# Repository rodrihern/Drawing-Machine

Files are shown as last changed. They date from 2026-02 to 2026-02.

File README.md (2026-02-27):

# Drawing Machine

Plotter de dibujo construido junto a 3 compañeros durante el secundario. La máquina mueve un marcador en los ejes X e Y usando motores paso a paso, y sube/baja el marcador con un servo, todo controlado por un Arduino con una CNC Shield.

## Hardware

- Arduino Uno
- CNC Shield con drivers A4988
- 2 motores paso a paso (ejes X e Y)
- 1 servo (eje Z, para subir/bajar el marcador)
- 2 finales de carrera (home X e Y)
- Estructura mecánica propia (ver carpeta `parts3d/`)

El shield fue diseñado en Altium (archivos en `shield/`) y es equivalente al **Arduino CNC Shield v3**

### Área de dibujo

- X: 0 – 228 mm
- Y: 0 – 244 mm

## Software

### Firmware (Arduino)

El archivo principal es [`src/drawing_machine.ino`](src/drawing_machine.ino).  
Recibe comandos G-code por puerto serie (9600 baud) y los ejecuta.  
Al iniciar, la máquina hace homing automático yendo al origen (0, 0) con los finales de carrera.

Parámetros configurables dentro del `.ino`:

| Parámetro | Valor por defecto | Descripción |
|---|---|---|
| `modoDePaso` | 16 (1/16 step) | Microstepping |
| `stepDelay` | `1000 / modoDePaso` | Velocidad de los motores |
| `StepsPerMillimeterX/Y` | `~50.4 steps/mm` | Calibración |
| `penZUp / penZDown` | 90° / 0° | Posición del servo |

### Envío del G-code (Python)

El script [`src/sender.py`](src/sender.py) lee un archivo G-code línea por línea y lo envía al Arduino por serial, esperando confirmación (`ok`) antes de enviar la siguiente línea.

Requiere la librería `pyserial`:

```bash
pip install pyserial
```

Antes de correrlo, ajustar el puerto COM en el script y pasarle la ruta al archivo G-code.

## Flujo de uso

1. **Generar el G-code** en Inkscape con el plugin 4xiDraw. Tutorial: https://www.youtube.com/watch?v=bhzCfIEzs0w

2. **Filtrar arcos** (convertir arcos a segmentos rectos): https://constant-flow.github.io/arc-breaker/

3. **Conectar el Arduino** Copiar y pegar el archivo gcode del dibujo en `drawing_to_send.txt` y correr el script Python:
   ```bash
   python src/sender.py
   ```

## Estructura del repositorio

```
src/        → Firmware Arduino y script Python
parts3d/    → Modelos 3D de las piezas
shield/     → Diseño del PCB (Altium)
drawings/   → G-codes e imágenes de dibujos realizados
```

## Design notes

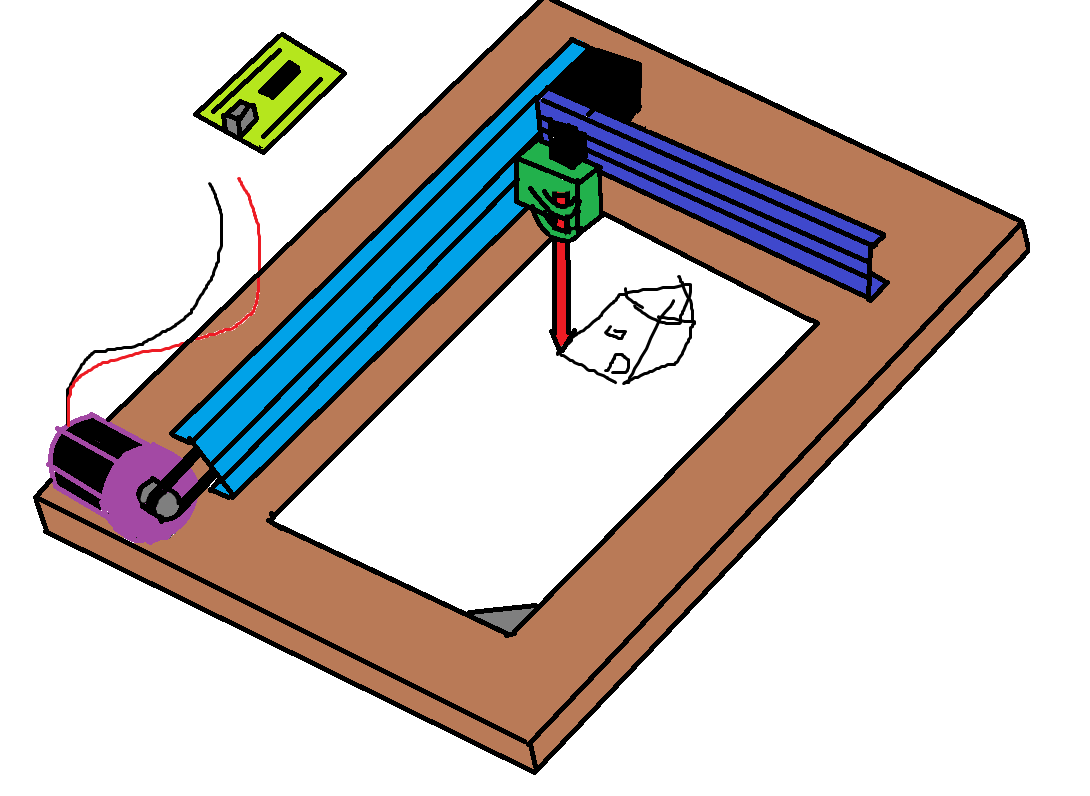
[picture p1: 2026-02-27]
design.png

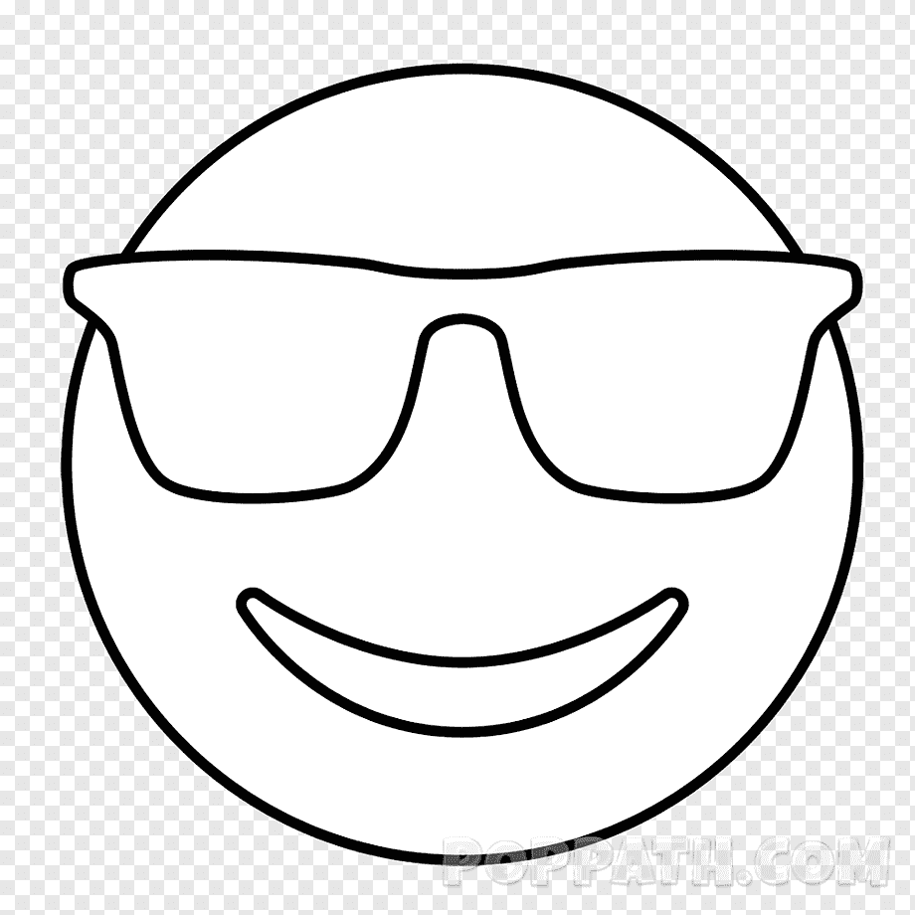
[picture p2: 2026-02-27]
drawings/carita con anteojos.png

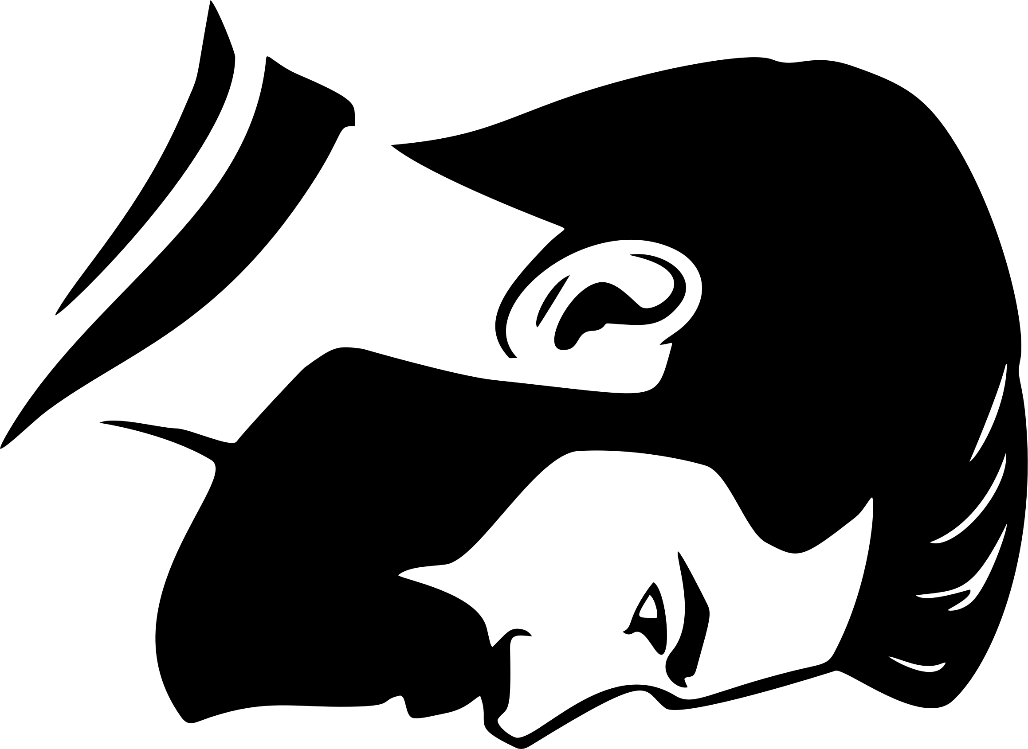
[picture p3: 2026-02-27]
drawings/Gaspi chad.png

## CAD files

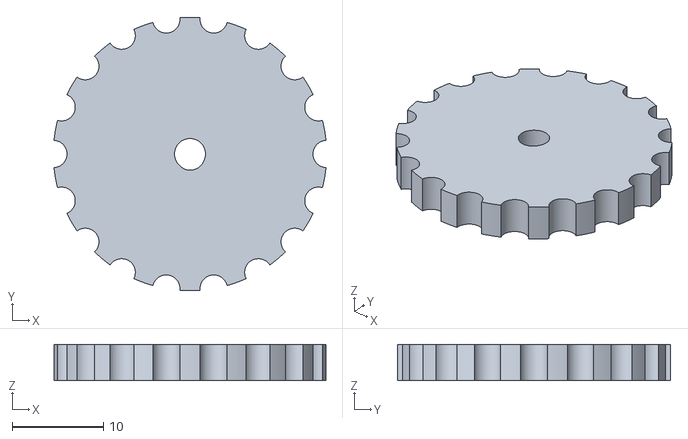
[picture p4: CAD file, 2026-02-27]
parts3d/bed levelling gear.stl
29.9 x 30.0 x 4.00

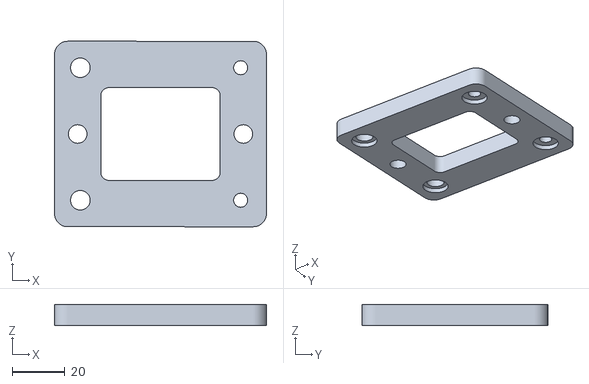
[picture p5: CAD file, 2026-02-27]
parts3d/Intersenction Bottom.stl
80.0 x 70.0 x 8.00

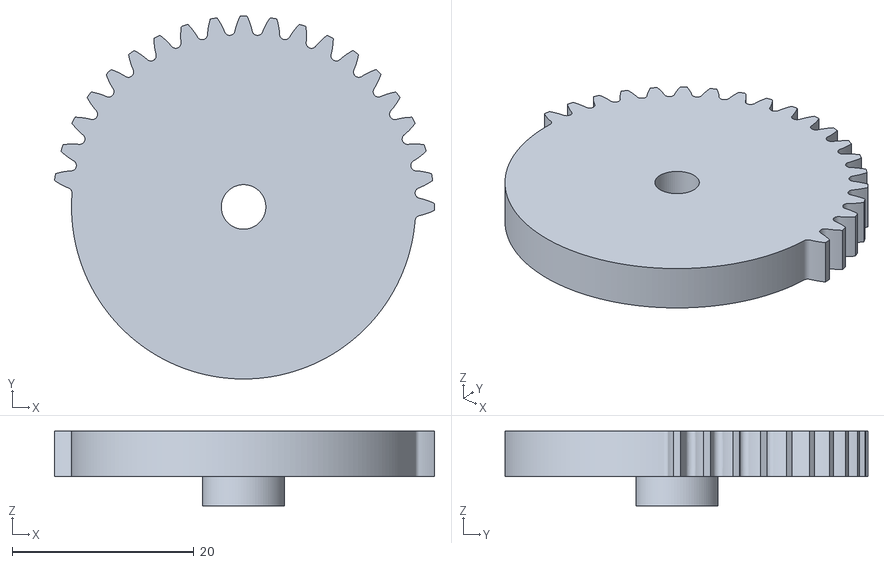
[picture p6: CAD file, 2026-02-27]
parts3d/gear.stl
41.8 x 39.9 x 8.20

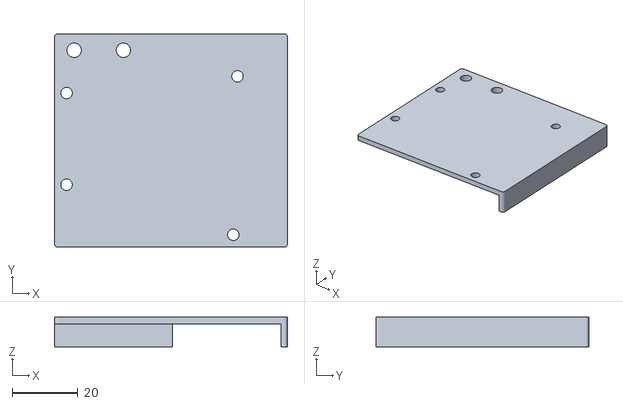
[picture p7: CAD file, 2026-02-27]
parts3d/arduino plate.stl
71.0 x 65.0 x 9.00

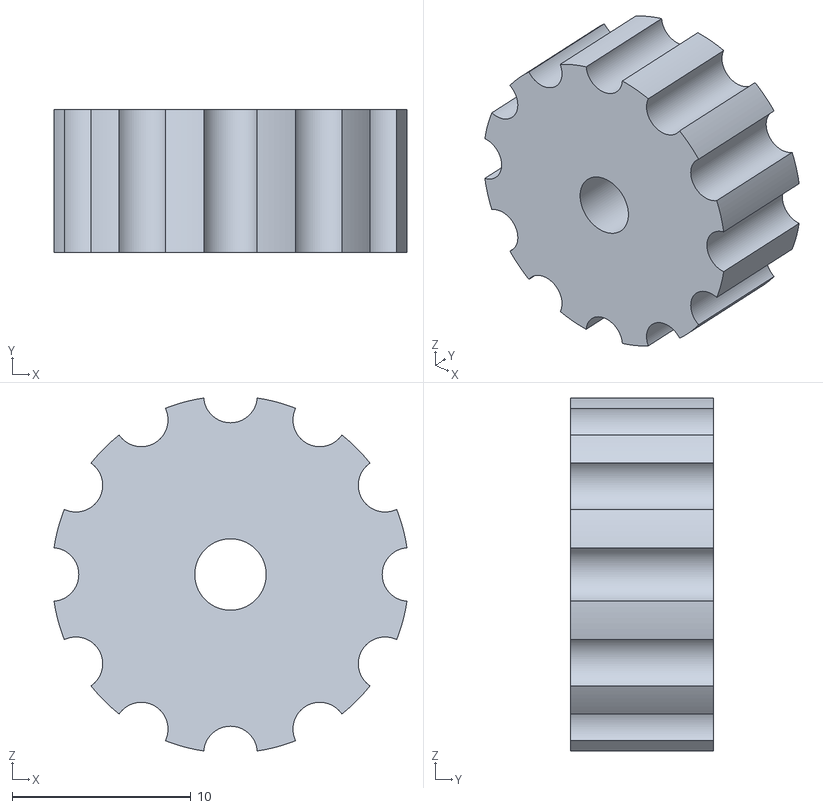
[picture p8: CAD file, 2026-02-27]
parts3d/knob.stl
19.8 x 8.00 x 19.8

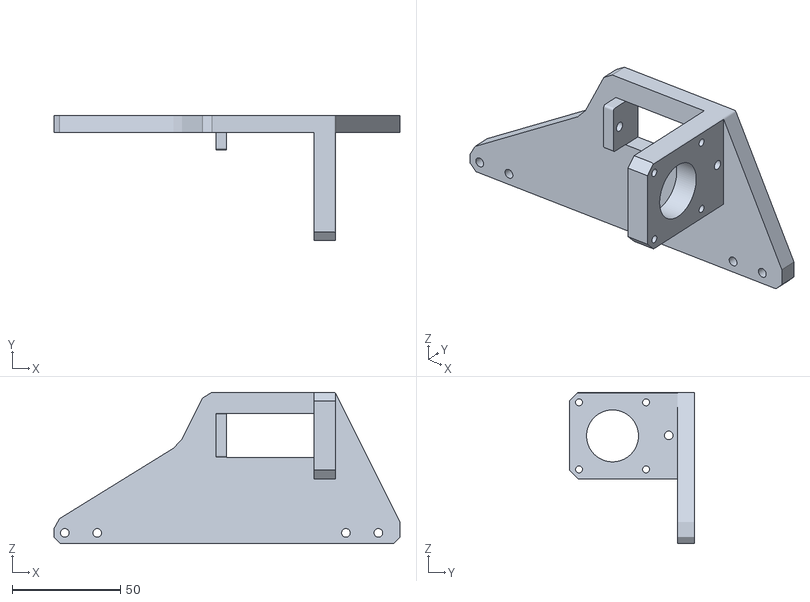
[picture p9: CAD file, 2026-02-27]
parts3d/base plate top.stl
160.0 x 58.0 x 70.0

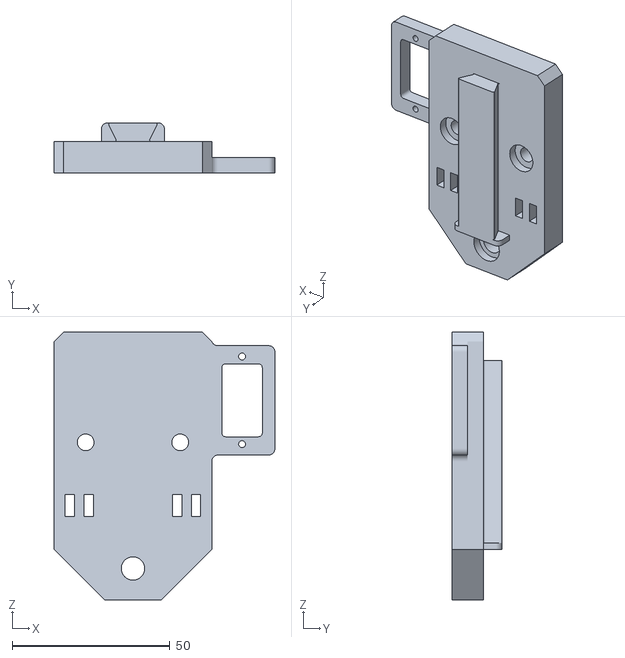
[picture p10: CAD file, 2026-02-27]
parts3d/x plate.stl
70.0 x 16.0 x 85.0

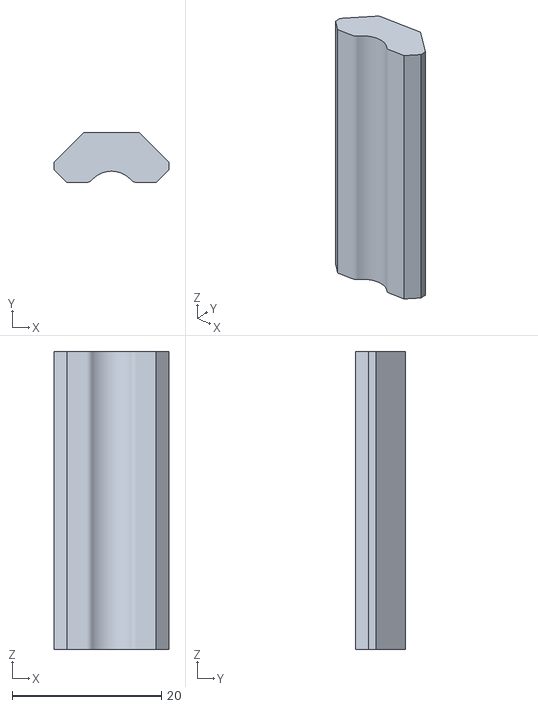
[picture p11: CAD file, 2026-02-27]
parts3d/pen holder clamp.stl
15.4 x 6.68 x 40.0

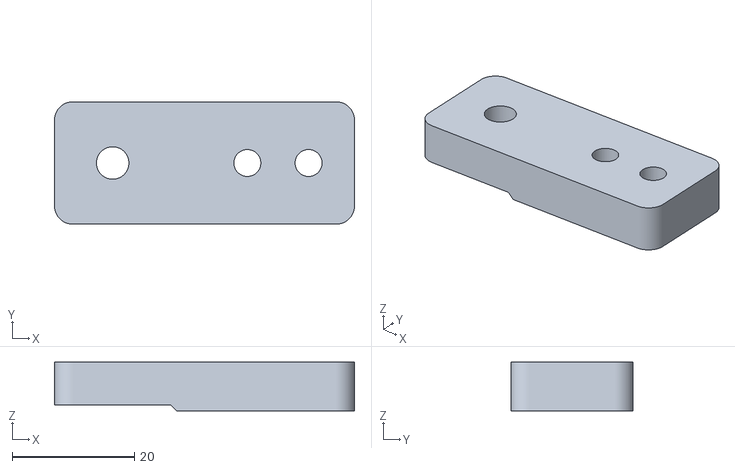
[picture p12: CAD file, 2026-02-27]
parts3d/x pulley plate.stl
49.0 x 20.0 x 8.00

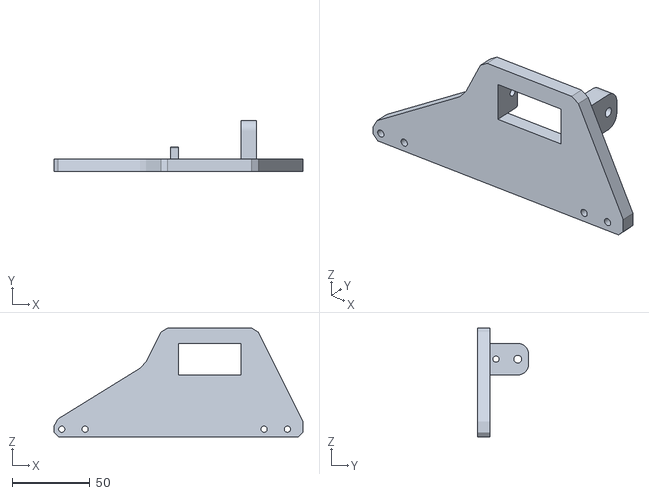
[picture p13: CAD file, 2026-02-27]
parts3d/base plate bottom.stl
160.0 x 33.0 x 70.0

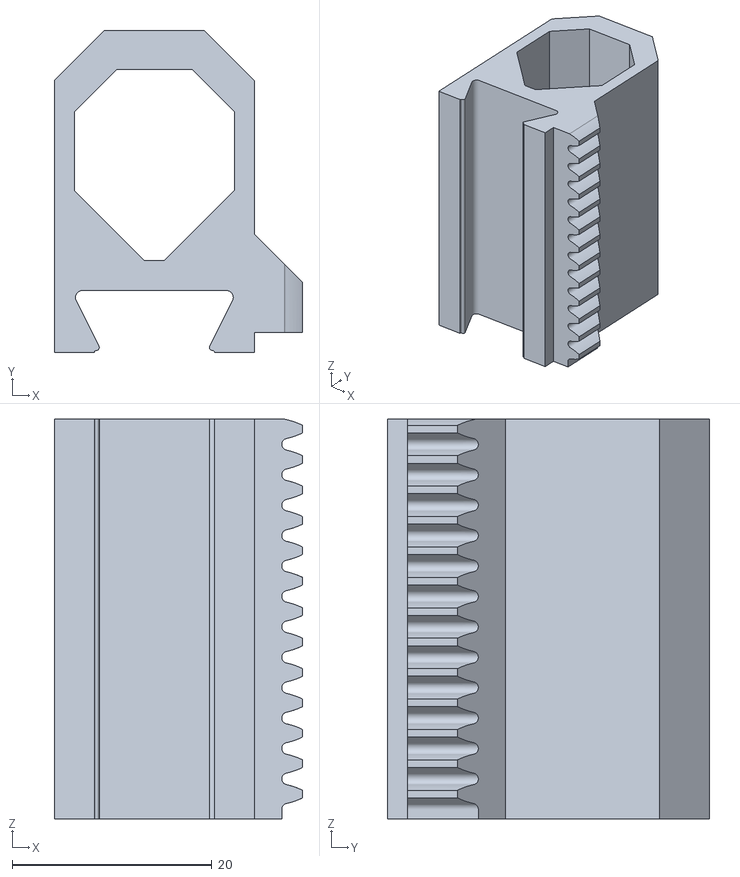
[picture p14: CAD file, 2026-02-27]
parts3d/pen holder.stl
24.8 x 32.2 x 40.0

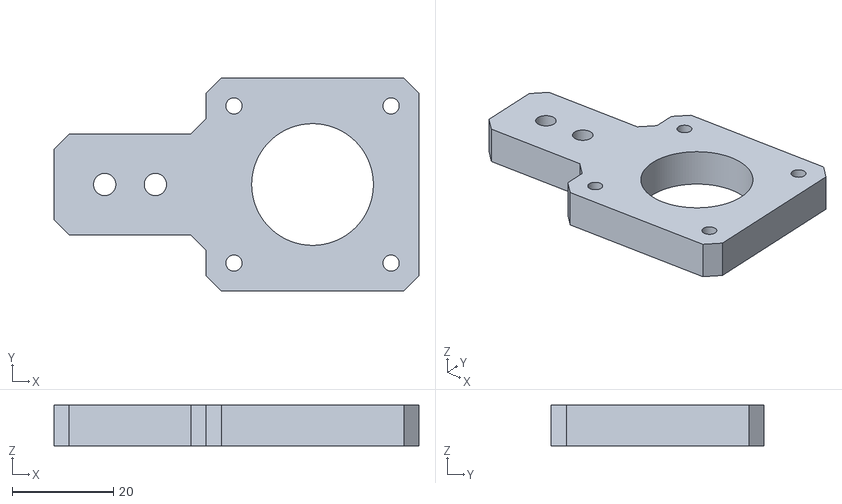
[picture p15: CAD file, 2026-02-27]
parts3d/x motor plate.stl
72.0 x 42.0 x 8.00

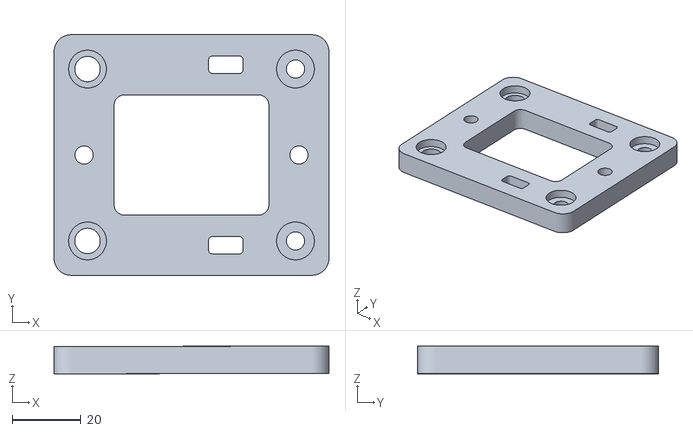
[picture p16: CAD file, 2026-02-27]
parts3d/Intersection Top.stl
80.0 x 70.0 x 8.00

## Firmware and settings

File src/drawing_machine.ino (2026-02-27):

#include <Servo.h>


#define LARGO_BUFFER 512

// Posicion del Servo para up y down
const int penZUp = 90;
const int penZDown = 0;

/*
 * El servo tiene que estar en un pin de pwm
 */

// Pines del servo
#define servoPin 11


// Pines de los drivers
#define step_x 2
#define step_y 8
#define dir_x 3
#define dir_y 7

/*
 *
 * PROBAR CON MICROSTEPING PARA EVITAR QUE SALTE PASOS
 * SE MUEVE MAS FLUIDO Y TIENE MAS TORQUE
 
 */
#define MS1 4
#define MS2 5
#define MS3 6

// fines de carrera
#define finCarrera_y 9
#define finCarrera_x 10


// settings para dibujar
int modoDePaso = 16; // 1 FULL STEP, 2 1/2 STEP, 4 1/4 STEP, 8 1/8 STEP, 16 1/16 STEP

const int stepsPorVuelta = 200*modoDePaso;
const int stepDelay = 1000 / modoDePaso;    // mientras mas chico, mas rapido gira. no usar valores menores a 500/modoDePaso
const int lineDelay = 0;
const int penDelay = 300;

Servo penServo;

struct posicion {
  float x; 
  float y; 
  float z;
  
};

// Posicion actual del amigo
struct posicion actuatorPos;




// Cuantos pasos para que se mueva 1mm
float StepsPerMillimeterX = 700.0/139.0 * modoDePaso;
float StepsPerMillimeterY = 700.0/139.0 * modoDePaso;

// Limites del dibujo, en mm
float Xmin = 0;
float Xmax = 228;
float Ymin = 0;
float Ymax = 244;
float Zmin = 0;
float Zmax = 1;

float Xpos = Xmax;
float Ypos = Ymin;
float Zpos = Zmax; 

// Poner en True para depurar.
boolean verbose = false;

//  Needs to interpret 
//  G1 for moving
//  G4 P300 (wait 150ms)
//  M300 S30 (pen down)
//  M300 S50 (pen up)
//  Discard anything with a (
//  Discard any other command!

char linea[ LARGO_BUFFER ];
char c;
int indice = 0;
bool esComentario = false, esPuntoComa = false;




void setup() {
  
  pinMode(servoPin, OUTPUT);

  pinMode(step_x, OUTPUT);
  pinMode(step_y, OUTPUT);
  pinMode(dir_x, OUTPUT);
  pinMode(dir_y, OUTPUT);

  pinMode(MS1, OUTPUT);
  pinMode(MS2, OUTPUT);
  pinMode(MS3, OUTPUT);

  pinMode(finCarrera_x, INPUT_PULLUP);
  pinMode(finCarrera_y, INPUT_PULLUP);

  
  Serial.begin( 9600 );
  Serial.setTimeout(1);
  
  penServo.attach(servoPin);
  penServo.write(penZUp);
  delay(100);

  //  Notifications!!!
  Serial.println("Drawing Machine AKA Borges esta vivito y coleando:)");
  Serial.print("X va desde "); 
  Serial.print(Xmin); 
  Serial.print(" hasta "); 
  Serial.print(Xmax); 
  Serial.println(" mm."); 
  Serial.print("Y va desde "); 
  Serial.print(Ymin); 
  Serial.print(" hasta "); 
  Serial.print(Ymax); 
  Serial.println(" mm."); 
  


  
  //seteamos el step
  tipo_step(modoDePaso);

  inicio();

  delay(100);

}

void loop() {
  // Serial reception - Mostly from Grbl, added semicolon support
    while ( Serial.available()>0 ) {
      c = Serial.read();
      if (( c == '\n') || (c == '\r') || (c=='B')) {             // End of line reached
        if ( indice > 0 ) {                        // Line is complete. Then execute!
          linea[ indice ] = '\0';                   // Terminate string
          if (verbose) { 
            Serial.print( "Received : "); 
            Serial.println( linea ); 
          }
          processIncomingLine( linea, indice );
          indice = 0;
        } 
        else { 
          if (verbose) { 
            Serial.print( "Received : "); 
            Serial.println( linea ); 
          }
        }
        esComentario = false;
        esPuntoComa = false;
        //Serial.println("ok");    
      } 
      else {
        if ( (esComentario) || (esPuntoComa) ) {   // Throw away all comment characters
          if ( c == ')' )  esComentario = false;     // End of comment. Resume line.
        } 
        else {
          if ( c <= ' ' ) {                           // Throw away whitepace and control characters
          } 
          else if ( c == '/' ) {                    // Block delete not supported. Ignore character.
          } 
          else if ( c == '(' ) {                    // Enable comments flag and ignore all characters until ')' or EOL.
            esComentario = true;
          } 
          else if ( c == ';' ) {
            esPuntoComa = true;
          } 
          else if ( indice >= LARGO_BUFFER-1 ) {
            Serial.println( "ERROR - lineBuffer overflow" );
            esComentario = false;
            esPuntoComa = false;
          } 
          else if ( c >= 'a' && c <= 'z' ) {        // Upcase lowercase
            linea[ indice++ ] = c-'a'+'A';
          } 
          else {
            linea[ indice++ ] = c;
          }
        }
      }
    }
}


void processIncomingLine( char* linea, int charNB ) {
  int currentIndex = 0;
  char buffer[ 64 ];                                 // Hope that 64 is enough for 1 parameter
  struct posicion newPos;

  newPos.x = 0.0;
  newPos.y = 0.0;

  //  Needs to interpret 
  //  G1 for moving
  //  G4 P300 (wait 150ms)
  //  G1 X60 Y30
  //  G1 X30 Y50
  //  M300 S30 (pen down)
  //  M300 S50 (pen up)
  //  Discard anything with a (
  //  Discard any other command!

  while( currentIndex < charNB ) {
    switch ( linea[ currentIndex++ ] ) {              // Select command, if any
    case 'U':
      penUp(); 
      break;
    case 'D':
      penDown(); 
      break;
    case 'G':
      buffer[0] = linea[ currentIndex++ ];          // /!\ Dirty - Only works with 2 digit commands
      //      buffer[1] = linea[ currentIndex++ ];
      //      buffer[2] = '\0';
      buffer[1] = '\0';

      switch ( atoi( buffer ) ){                   // Select G command
      case 0:                                   // G00 & G01 - Movement or fast movement. Same here
      case 1:
        // /!\ Dirty - Suppose that X is before Y
        char* indexX = strchr( linea+currentIndex, 'X' );  // Get X/Y position in the string (if any)
        char* indexY = strchr( linea+currentIndex, 'Y' );
        if ( indexY <= 0 ) {
          newPos.x = atof( indexX + 1); 
          newPos.y = actuatorPos.y;
        } 
        else if ( indexX <= 0 ) {
          newPos.y = atof( indexY + 1);
          newPos.x = actuatorPos.x;
        } 
        else {
          newPos.y = atof( indexY + 1);
          *indexY = '\0';
          newPos.x = atof( indexX + 1);
        }
        draw_line(newPos.x, newPos.y );
        //        Serial.println("ok");
        actuatorPos.x = newPos.x;
        actuatorPos.y = newPos.y;
        break;
      }
      break;
    case 'M':
      buffer[0] = linea[ currentIndex++ ];        // /!\ Dirty - Only works with 3 digit commands
      buffer[1] = linea[ currentIndex++ ];
      buffer[2] = linea[ currentIndex++ ];
      buffer[3] = '\0';
      switch ( atoi( buffer ) ){
      case 300:
        {
          char* indexS = strchr( linea+currentIndex, 'S' );
          float Spos = atof( indexS + 1);
          //         Serial.println("ok");
          if (Spos == 30) { 
            penDown(); 
          }
          if (Spos == 50) { 
            penUp(); 
          }
          break;
        }
      case 114:                                // M114 - Repport position
        Serial.print( "Absolute position : X = " );
        Serial.print( actuatorPos.x );
        Serial.print( "  -  Y = " );
        Serial.println( actuatorPos.y );
        break;
      default:
        Serial.print( "Command not recognized : M");
        Serial.println( buffer );
      }
    }
  }



}

void tipo_step(int modo){
  if (modo == 2) {
    digitalWrite(MS1, HIGH);
    digitalWrite(MS2, LOW);
    digitalWrite(MS3, LOW);
  }
  else if (modo == 4){
    digitalWrite(MS1, LOW);
    digitalWrite(MS2, HIGH);
    digitalWrite(MS3, LOW);
  }
  else if (modo == 8) {
    digitalWrite(MS1, HIGH);
    digitalWrite(MS2, HIGH);
    digitalWrite(MS3, LOW);
  }
  else if (modo == 16) {
    digitalWrite(MS1, HIGH);
    digitalWrite(MS2, HIGH);
    digitalWrite(MS3, HIGH);
  }
  else {
    digitalWrite(MS1, LOW);
    digitalWrite(MS2, LOW);
    digitalWrite(MS3, LOW);
    modoDePaso = 1;
    
  }
}


void draw_line(float x1,float y1) {

  if (verbose)
  {
    Serial.print("fx1, fy1: ");
    Serial.print(x1);
    Serial.print(",");
    Serial.print(y1);
    Serial.println("");
  }  

  //  Bring instructions within limits
  if (x1 >= Xmax) { 
    x1 = Xmax; 
  }
  if (x1 <= Xmin) { 
    x1 = Xmin; 
  }
  if (y1 >= Ymax) { 
    y1 = Ymax; 
  }
  if (y1 <= Ymin) { 
    y1 = Ymin; 
  }

  if (verbose)
  {
    Serial.print("Xpos, Ypos: ");
    Serial.print(Xpos);
    Serial.print(",");
    Serial.print(Ypos);
    Serial.println("");
  }

  if (verbose)
  {
    Serial.print("x1, y1: ");
    Serial.print(x1);
    Serial.print(",");
    Serial.print(y1);
    Serial.println("");
  }

  //  Convert coordinates to steps
  //x1 = (int)(x1*StepsPerMillimeterX);
  //y1 = (int)(y1*StepsPerMillimeterY);
  float x0 = Xpos;
  float y0 = Ypos;

  //  Let's find out the change for the coordinates
  float dx = abs(x1-x0);
  float dy = abs(y1-y0);

  if (verbose)
  {
    Serial.print("dx, dy:");
    Serial.print(dx);
    Serial.print(",");
    Serial.print(dy);
    Serial.println("");
  }

  if (verbose)
  {
    Serial.print("Going to (");
    Serial.print(x1);
    Serial.print(",");
    Serial.print(y1);
    Serial.println(")");
  }
  Serial.println("ok");

  dx *= StepsPerMillimeterX;
  dy *= StepsPerMillimeterY;

  if (x0<x1) {
    digitalWrite(dir_x, HIGH);
  }
  else {
    digitalWrite(dir_x, LOW);
  }

  if (y0<y1) {
    digitalWrite(dir_y, LOW);
  }
  else {
    digitalWrite(dir_y, HIGH);
  }

  long i;
  long over = 0;

  if (dx > dy) {
    for (i=0; i<dx; ++i) {

      digitalWrite(step_x, HIGH);
      delayMicroseconds(stepDelay);
      digitalWrite(step_x, LOW);
      delayMicroseconds(stepDelay);

      
      over+=dy;
      if (over>=dx) {
        over-=dx;

        digitalWrite(step_y, HIGH);
        delayMicroseconds(stepDelay);
        digitalWrite(step_y, LOW);
        delayMicroseconds(stepDelay);
 
      }
    delayMicroseconds(stepDelay);
    }
  }
  else {
    for (i=0; i<dy; ++i) {

      digitalWrite(step_y, HIGH);
      delayMicroseconds(stepDelay);
      digitalWrite(step_y, LOW);
      delayMicroseconds(stepDelay);
      
      over+=dx;
      if (over>=dy) {
        over-=dy;

        digitalWrite(step_x, HIGH);
        delayMicroseconds(stepDelay);
        digitalWrite(step_x, LOW);
        delayMicroseconds(stepDelay);
        
      }
      delayMicroseconds(stepDelay);
    }    
  }

  

  //  Delay before any next lines are submitted
  delay(lineDelay);
  //  Update the positions
  Xpos = x1;
  Ypos = y1;
}

//  Raises pen
void penUp() { 
  penServo.write(penZUp); 
  delay(penDelay); 
  Zpos=Zmax; 

  if (verbose) { 
    Serial.println("Pen up!"); 
    
  } 
}
//  Lowers pen
void penDown() { 
  penServo.write(penZDown); 
  delay(penDelay); 
  Zpos=Zmin; 

  if (verbose) { 
    Serial.println("Pen down."); 
    
    
  } 
}
  

void inicio() {
  penUp(); 
  digitalWrite(dir_x, HIGH);
  digitalWrite(dir_y, HIGH);
  
  while (digitalRead(finCarrera_x) == HIGH) {
    digitalWrite(step_x, HIGH);
    delayMicroseconds(stepDelay);
    digitalWrite(step_x, LOW);
    delayMicroseconds(stepDelay);
  }

  while (digitalRead(finCarrera_y) == HIGH) {
    digitalWrite(step_y, HIGH);
    delayMicroseconds(stepDelay);
    digitalWrite(step_y, LOW);
    delayMicroseconds(stepDelay);
  }
}

  

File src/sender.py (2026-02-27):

import serial

PORT = 'COM6' # set as needed

arduino = serial.Serial(port=PORT, baudrate=9600)

file1 = open('./drawing_to_send.txt', 'r')
Lines = file1.readlines()


for i in range(3):
    print(arduino.readline().decode('utf-8').rstrip())


def write(coord):
    arduino.write(bytes(coord, 'utf-8'))

count = 0
for line in Lines:
    count += 1
    if "X" in line or "Y" in line or "M" in line:
        write(line)
        print(line)
        if "X" in line or "Y" in line:
            while arduino.readline().decode('utf-8').rstrip() != "ok":
                print(arduino.readline().decode('utf-8').rstrip())
    
